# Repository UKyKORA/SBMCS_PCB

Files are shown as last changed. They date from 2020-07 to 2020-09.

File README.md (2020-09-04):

# Small Bot Motor Control Shield
This PCB makes building an advanced robot very simple. An onboard 32 bit ARM processor coordinates the control of 2 motors, as well as monitoring encoders on these motors for wheel odometry for the robot. There is a 9 axis IMU on the board to provide inertial odometry as well. a 5v @5A regulator provides enough power for most single board computers

### Board renders
<p>
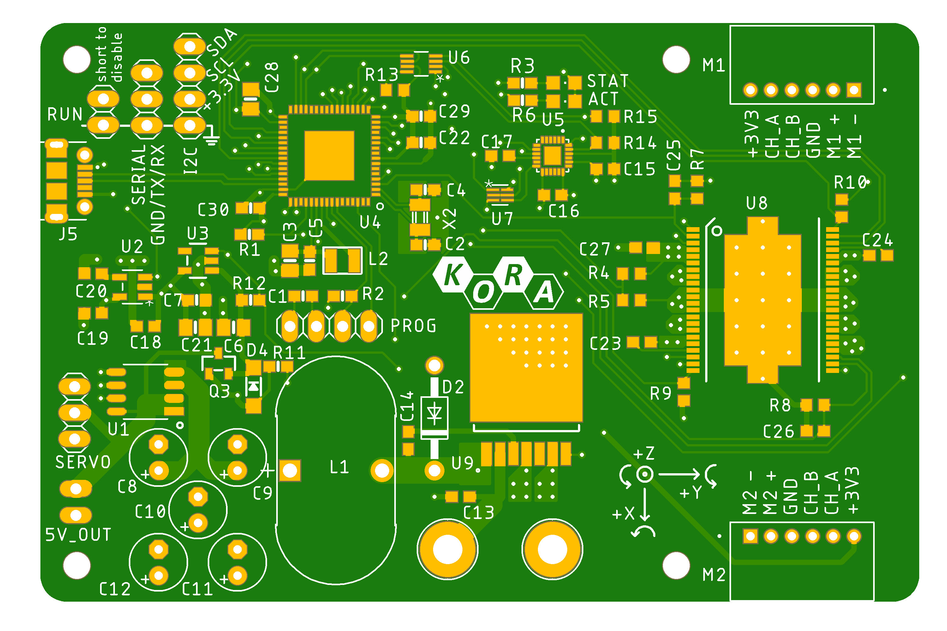
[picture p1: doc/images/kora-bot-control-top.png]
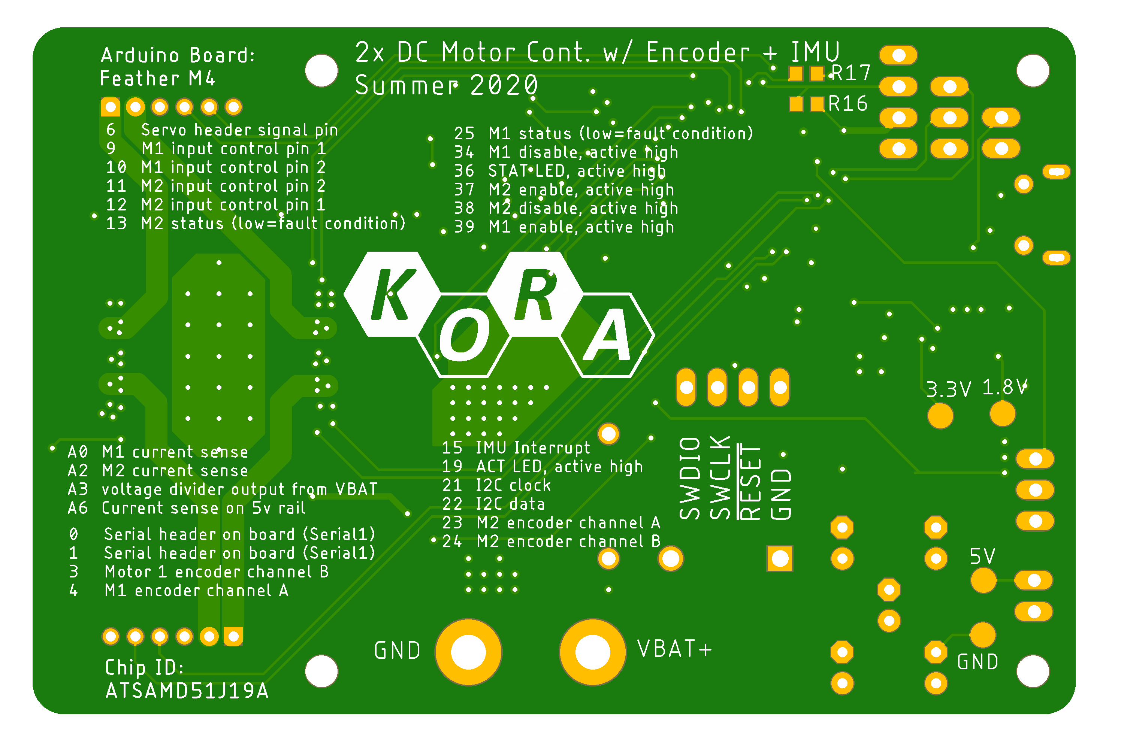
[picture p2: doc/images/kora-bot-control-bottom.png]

</p>

### Assembled boards
<p>

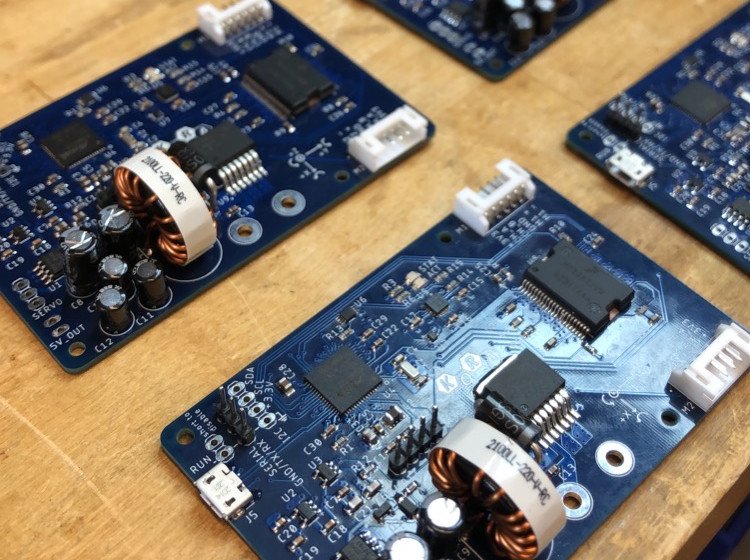
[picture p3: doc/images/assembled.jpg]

</p>

### Demonstration

[https://youtu.be/KzK6t1kKt98](https://youtu.be/KzK6t1kKt98)

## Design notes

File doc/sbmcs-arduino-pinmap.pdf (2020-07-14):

DEVICE PIN | ARDUINO PIN | NET | COMMENT
PA02 | A0 (14) | IM1_SENSE | motor 1 current sense, 0.24% of motor current is output across a 270 ohm resistor
PA05 | A1 (15) | INT | ICM20948 imu interrupt pin
PA06 | A5 (19) | ACT | ACT LED, active high
PA08 | 36 | STAT | STAT LED, active high
PA09 | 37 | EN/D4 | M2 enable pin, active high
PA10 | 38 | D3 | M2 disable pin, active high
PA11 | 39 | EN/D2 | M1 enable pin, active high
PA12 | 22 | SDA | I2C data
PA13 | 21 | SCL | I2C clock
PA14 | 4 | M1_ENC_A | motor 1 encoder channel a
PA17 | 25 | M1_STATUS | status (low=fault condition)
PA18 | 6 | SERVO | servo header signal pin
PA19 | 9 | IN1 | M1 input control pin 1
PA20 | 10 | IN2 | M1 input control pin 2
PA21 | 11 | IN4 | M2 input control pin 2
PA22 | 12 | IN3 | M2 input control pin 1
PA23 | 13 | M2_STATUS | status (low=fault condition)
PB01 | A6 (20) | I5V_SENSE | current sense on 5v rail
PB08 | A2 (16) | IM2_SENSE | motor 2 current sense, 0.24% of motor current is output across a 270 ohm resistor
PB09 | A3 (17) | VBAT_SENSE | voltage divider output from battery sensing.300k to vbat, 85k to gnd
PB10 | 34 | D1 | disable m1 (active high, high=motor pins are three stated
PB11 | 35 | M1_ENC_B | motor 1 encoder channel b
PB17 | 0 | SERIAL_RX | serial header on board (Serial1 object in arduino)
PB16 | 1 | SERIAL_TX | serial header on board (Serial1 object in arduino)
PB22 | 23 | M2_ENC_A | motor 2 encoder channel a
PB23 | 24 | M2_ENC_B | motor 2 encoder channel b

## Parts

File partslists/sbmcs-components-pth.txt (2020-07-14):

# through hole parts for korabot motor control shield

H1       MOUNT-PAD-ROUND2.8 MOUNT-PAD-ROUND2.8        2,8-PAD                holes              4
H2       MOUNT-PAD-ROUND2.8 MOUNT-PAD-ROUND2.8        2,8-PAD                holes              4

5V_OUT                      PINHD-1X2                 1X02                   pinhead            4
PROG                        PINHD-1X4                 1X04                   pinhead            1
I2C                         PINHD-1X4                 1X04                   pinhead            1
RUN                         PINHD-1X2                 1X02                   pinhead            4
SERIAL                      PINHD-1X3                 1X03                   pinhead            1
SERVO                       PINHD-1X3                 1X03                   pinhead            1
 M1       S6B-PH-K-S(LF)(SN) S6B-PH-K-S(LF)(SN)        JST_S6B-PH-K-S(LF)(SN) S6B-PH-K-S_LF__SN_ 2
 M2       S6B-PH-K-S(LF)(SN) S6B-PH-K-S(LF)(SN)        JST_S6B-PH-K-S(LF)(SN) S6B-PH-K-S_LF__SN_ 2

 C8       180uF              CPOL-USE2.5-6             E2,5-6                 adafruit           4
 C9       180uF              CPOL-USE2.5-6             E2,5-6                 adafruit           4
 C10      15uF               CPOL-USE2.5-6             E2,5-6                 adafruit           4
 C11      15uF               CPOL-USE2.5-6             E2,5-6                 adafruit           4
 C12      15uF               CPOL-USE2.5-6             E2,5-6                 adafruit           4

 L1       2100LL-220-V-RC    2100LL-220-V-RC           IND_2100LL_42_V        TI3VRegulator      4

 D2       1N4004             1N4004                    DO41-10                diode              4

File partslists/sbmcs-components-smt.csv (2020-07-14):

kora-bot-shield BOM
Item # | Ref. Des | Qty. | Mfg. Part # (DIGIKEY) | Description/Value | Package | Type
1 | STAT | 1 | LH R974-LP-1 | RED LED | 0805 | SMT
2 | ACT | 1 | LG R971-KN-1 | GREEN LED | 0805 | SMT
3 | C1,C5,C7,C22,C25,C26,C29,C30 | 8 | CL10A105KL8NNNC | 1 UF CER CAP | 0603 | SMT
4 | C2,C4 | 2 | C0603C220J8GAC7867 | 22 PF CER CAP | 0603 | SMT
5 | C3,C6,C21,C28 | 4 | C2012X5R1E106M125AB | 10 UF CER CAP | 0805 | SMT
6 | C13 | 1 | C1608X7R1H474K080AC | 0.47 UF CER CAP | 0603 | SMT
7 | C14,C20 | 2 | C1608C0G1V103J080AC | 10000 PF CER CAP | 0603 | SMT
8 | C15,C16,C17,C18,C27 | 5 | C0603C104Z3VACTU | 0.1 UF CER CAP | 0603 | SMT
9 | C19 | 1 | GRM188R71A225KE15D | 2.2 UF CER CAP | 0603 | SMT
10 | C23,C24 | 2 | CC0603KRX7R9BB333 | 0.033 UF CER CAP | 0603 | SMT
11 | U6 | 1 | PCA9306DCUR | IC TRNSLTR BIDIRECTIONAL | 8VSSOP | SMT
12 | U5 | 1 | ICM-20948 | IMU ACCEL/GYRO/COMPI2C/SPI | 24QFN | SMT
13 | U3 | 1 | AP2112K-3.3TRG1 | IC REG LINEAR 3.3V 600MA | SOT25 | SMT
14 | U2 | 1 | LP2985IM5-1.8/NOPB | IC REG LINEAR 1.8V 150MA | SOT23-5 | SMT
15 | U1 | 1 | ACS724LLCTR-05AB-T | SENSOR CURRENT HALL | 8-SOIC | SMT
16 | U8 | 1 | MC33932VWR2 | IC MOTOR DRIVER | 44HSOP | SMT
17 | L2 | 1 | CBC2518T100M | FIXED IND 10UH 680MA 468 MOHM | 1007 | SMT
18 | J5 | 1 | 1050170001 | CONN RCPT USB2.0 MICRO B SMD R/A | N/A | SMT
19 | U9 | 1 | LM2678SX-5.0/NOPB | IC REG BUCK 5V 5A | TO263-7 | SMT
20 | D4 | 1 | MBR120VLSFT3G | DIODE SCHOTTKY 20V 1A | SOD123FL | SMT
21 | U4 | 1 | ‎ATSAMD51J19A-MUT | IC MCU 32BIT 512KB FLASH | 64VQFN | SMT
22 | U7 | 1 | SN74LVC1T45DRLR | IC TRNSLTR BIDIRECTIONAL | 6SOT | SMT
23 | Q3 | 1 | DMP3056L-7 | MOSFET P-CH 30V 4.3A | SOT23 | SMT
24 | X2 | 1 | ECS-.327-12.5-34B-TR | CRYSTAL 32.7680KHZ 12.5PF SMD | N/A (3.2mm x 1.5mm) | SMT
25 | R1,R2,R12 | 3 | RC0603JR-0710KL | RES SMD 10K OHM 5% 1/10W | 0603 | SMT
26 | R3,R6 | 2 | RC0603JR-07470RL | RES SMD 470 OHM 5% 1/10W | 0603 | SMT
27 | R11 | 1 | RR0816P-104-D | RES SMD 100K OHM 0.5% 1/16W | 0603 | SMT
28 | R13 | 1 | RC0603FR-07200KL | RES SMD 200K OHM 1% 1/10W | 0603 | SMT
29 | R4 | 1 | RR0816P-304-D | RES SMD 300K OHM 0.5% 1/16W | 0603 | SMT
30 | R14,R15 | 2 | ERJ-3GEYJ222V | RES SMD 2.2K OHM 5% 1/10W | 0603 | SMT
31 | R7.R8,R9,R10 | 4 | CRGCQ0603F270R | RES SMD 270 OHM 1% | 0603 | SMT
32 | R5 | 1 | RC0603FR-0784K5L | RES SMD 84.5K OHM 1% 1/10W | 0603 | SMT

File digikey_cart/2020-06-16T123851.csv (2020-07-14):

Index | Quantity | Part Number | Manufacturer Part Number | Description | Customer Reference | Available | Backorder | Unit Price | Extended Price USD
1 | 11 | 475-1410-1-ND | LG R971-KN-1 | LED GREEN DIFFUSED 0805 SMD |  | 11 | 0 | 0.19100 | 2.10
2 | 11 | 475-1415-1-ND | LH R974-LP-1 | LED RED DIFFUSED 0805 SMD |  | 11 | 0 | 0.19100 | 2.10
3 | 11 | ATSAMD51J19A-MUTCT-ND | ATSAMD51J19A-MUT | IC MCU 32BIT 512KB FLASH 64VQFN |  | 11 | 0 | 4.34000 | 47.74
4 | 22 | 399-15378-1-ND | C0603C220J8GAC7867 | CAP CER 22PF 10V NP0 0603 |  | 22 | 0 | 0.12600 | 2.77
5 | 44 | 445-5985-1-ND | C2012X5R1E106M125AB | CAP CER 10UF 25V X5R 0805 |  | 44 | 0 | 0.26600 | 11.70
6 | 11 | 620-ACS724LLCTR-05AB-TCT-ND | ACS724LLCTR-05AB-T | SENSOR CURRENT HALL |  | 11 | 0 | 4.19500 | 46.15
7 | 22 | 399-7842-1-ND | C0603C103M5RACTU | CAP CER 10000PF 50V X7R 0603 |  | 22 | 0 | 0.03500 | 0.77
8 | 11 | 445-5952-1-ND | C1608X7R1H474K080AC | CAP CER 0.47UF 50V X7R 0603 |  | 11 | 0 | 0.19000 | 2.09
9 | 22 | 311-1429-1-ND | CC0603KRX7R9BB333 | CAP CER 0.033UF 50V X7R 0603 |  | 22 | 0 | 0.05800 | 1.28
10 | 11 | 296-20629-1-ND | SN74LVC1T45DRLR | IC TRNSLTR BIDIRECTIONAL 6SOT |  | 11 | 0 | 0.49500 | 5.45
11 | 11 | MBR120VLSFT3GOSCT-ND | MBR120VLSFT3G | DIODE SCHOTTKY 20V 1A SOD123FL |  | 11 | 0 | 0.31200 | 3.43
12 | 11 | LM2678SX-5.0/NOPBCT-ND | LM2678SX-5.0/NOPB | IC REG BUCK 5V 5A TO263-7 |  | 11 | 0 | 5.23600 | 57.60
13 | 11 | WM1399CT-ND | 1050170001 | CONN RCPT USB2.0 MICRO B SMD R/A |  | 11 | 0 | 0.80100 | 8.81
14 | 11 | 587-1613-1-ND | CBC2518T100M | FIXED IND 10UH 680MA 468 MOHM |  | 11 | 0 | 0.20700 | 2.28
15 | 11 | 568-15069-1-ND | MC33932VWR2 | IC MOTOR DRIVER PAR 44HSOP |  | 11 | 0 | 13.03800 | 143.42
16 | 11 | XC1617CT-ND | ECS-.327-12.5-34B-TR | CRYSTAL 32.7680KHZ 12.5PF SMD |  | 11 | 0 | 0.44800 | 4.93
17 | 11 | 490-4520-1-ND | GRM188R71A225KE15D | CAP CER 2.2UF 10V X7R 0603 |  | 11 | 0 | 0.18500 | 2.04
18 | 11 | DMP3056L-7DICT-ND | DMP3056L-7 | MOSFET P-CH 30V 4.3A SOT23 |  | 11 | 0 | 0.31300 | 3.44
19 | 11 | 296-17988-1-ND | PCA9306DCUR | IC TRNSLTR BIDIRECTIONAL 8VSSOP |  | 11 | 0 | 0.58100 | 6.39
20 | 11 | AP2112K-3.3TRG1DICT-ND | AP2112K-3.3TRG1 | IC REG LINEAR 3.3V 600MA SOT25 |  | 11 | 0 | 0.35500 | 3.91
21 | 11 | 1428-1123-1-ND | ICM-20948 | IMU ACCEL/GYRO/COMPI2C/SPI 24QFN |  | 11 | 0 | 6.26700 | 68.94
22 | 33 | 311-10KGRCT-ND | RC0603JR-0710KL | RES SMD 10K OHM 5% 1/10W 0603 |  | 33 | 0 | 0.01900 | 0.63
23 | 22 | 311-470GRCT-ND | RC0603JR-07470RL | RES SMD 470 OHM 5% 1/10W 0603 |  | 22 | 0 | 0.01900 | 0.42
24 | 11 | RR08P100KDCT-ND | RR0816P-104-D | RES SMD 100K OHM 0.5% 1/16W 0603 |  | 11 | 0 | 0.09300 | 1.02
25 | 11 | 311-200KHRCT-ND | RC0603FR-07200KL | RES SMD 200K OHM 1% 1/10W 0603 |  | 11 | 0 | 0.02300 | 0.25
26 | 11 | RR08P300KDCT-ND | RR0816P-304-D | RES SMD 300K OHM 0.5% 1/16W 0603 |  | 11 | 0 | 0.09300 | 1.02
27 | 22 | P2.2KGCT-ND | ERJ-3GEYJ222V | RES SMD 2.2K OHM 5% 1/10W 0603 |  | 22 | 0 | 0.04500 | 0.99
28 | 11 | 311-84.5KHRCT-ND | RC0603FR-0784K5L | RES SMD 84.5K OHM 1% 1/10W 0603 |  | 11 | 0 | 0.02300 | 0.25
29 | 55 | 399-1100-1-ND | C0603C104Z3VACTU | CAP CER 0.1UF 25V Y5V 0603 |  | 55 | 0 | 0.03200 | 1.76
30 | 88 | 1276-1861-1-ND | CL10A105KL8NNNC | CAP CER 1UF 35V X5R 0603 |  | 88 | 0 | 0.12900 | 11.35
31 | 22 | LP2985IM5-1.8/NOPBCT-ND | LP2985IM5-1.8/NOPB | IC REG LINEAR 1.8V 150MA SOT23-5 |  | 22 | 0 | 0.66700 | 14.67
32 | 44 | A129681CT-ND | CRGCQ0603F270R | CRGCQ 0603 270R 1% |  | 44 | 0 | 0.03000 | 1.32
33 | 22 | 1189-3642-ND | 25ZLQ180MEFC6.3X11 | CAP ALUM 180UF 20% 25V T/H |  | 22 | 0 | 0.20700 | 4.55
34 | 33 | P15801CT-ND | EEA-GA1E150H | CAP ALUM 15UF 20% 25V RADIAL |  | 33 | 0 | 0.18500 | 6.11
35 | 11 | 2100LL-220-V-RC-ND | 2100LL-220-V-RC | FIXED IND 22UH 7.5A 12 MOHM TH |  | 11 | 0 | 3.20900 | 35.30
36 | 11 | 1655-1921-1-ND | 90SQ045TA | DIODE SCHOTTKY 45V 9A DO201AD |  | 11 | 0 | 0.34000 | 3.74
37 | 22 | 455-1723-ND | S6B-PH-K-S(LF)(SN) | CONN HEADER R/A 6POS 2MM |  | 22 | 0 | 0.28500 | 6.27

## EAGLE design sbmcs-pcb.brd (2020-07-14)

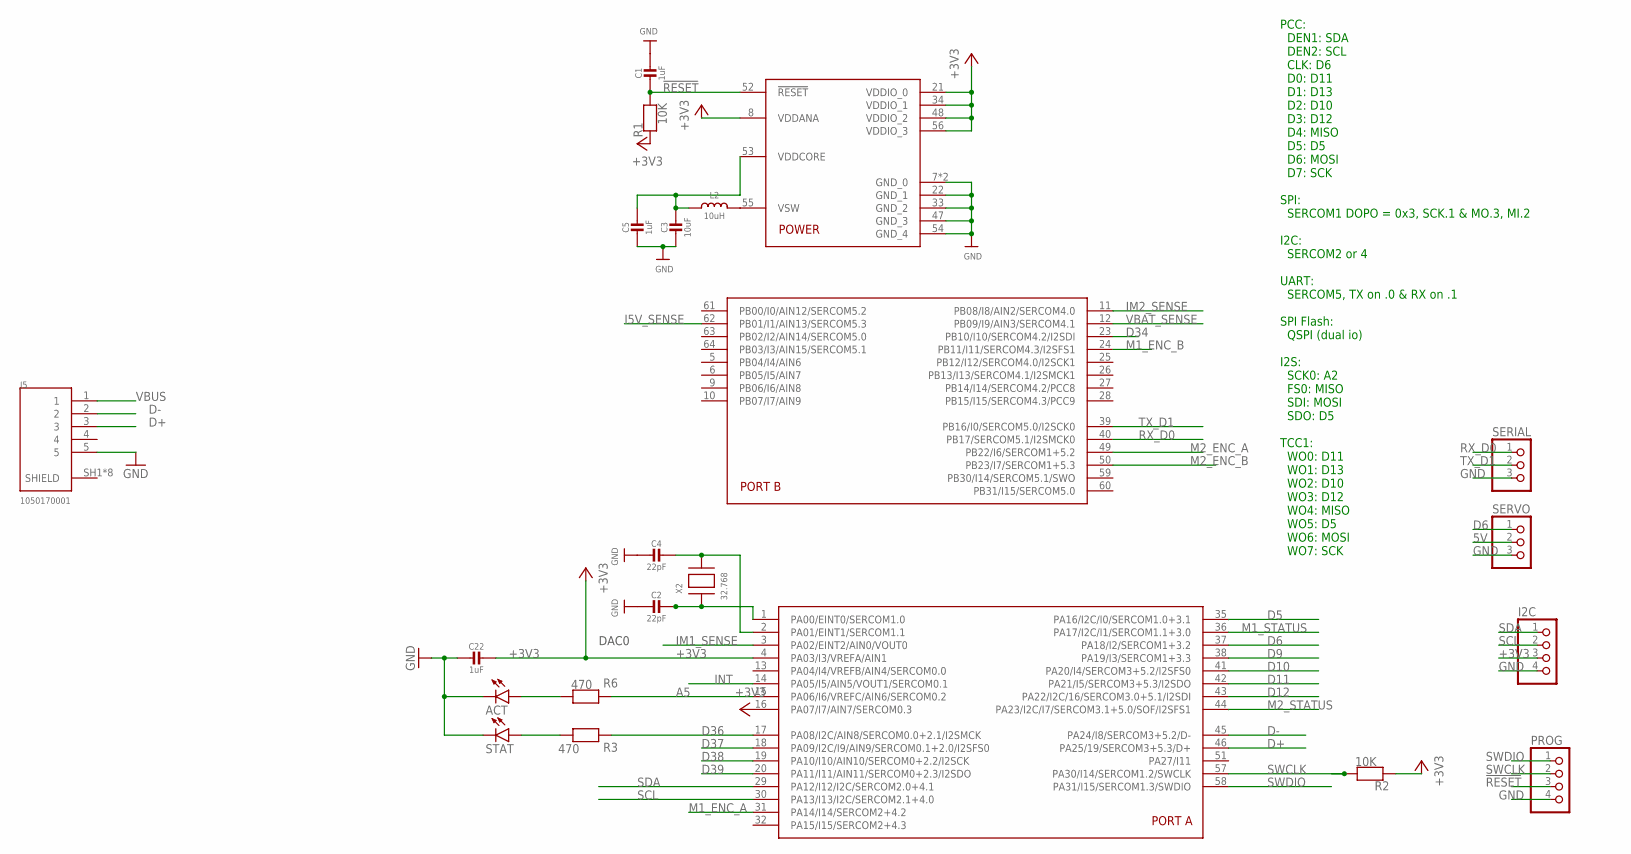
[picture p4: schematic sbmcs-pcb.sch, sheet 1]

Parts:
ACT: LEDCHIPLED_0805; CHIPLED_0805
C1, C5, C22: 1uF; 0603-NO
C2, C4: 22pF; 0603-NO
C3: 10uF; 0805-NO
I2C: PINHD-1X4; 1X04
J5: 1050170001; MOLEX_1050170001
L2: 10uH; INDUCTOR_1007
PROG: PINHD-1X4; 1X04
R1, R2: 10K; 0603-NO
R3, R6: 470; 0603-NO
SERIAL: PINHD-1X3; 1X03
SERVO: PINHD-1X3; 1X03
STAT: LEDCHIPLED_0805; CHIPLED_0805
U4: ATSAMD51J; PQFN64-1
X2: 32.768; XTAL3215

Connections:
5V: SERVO.2; also elsewhere on the board
!RESET: C1.2, PROG.3, R1.2, U4.52 (!RESET)
+3V3: C22.1, I2C.3, R1.1, R2.1, U4.4 (PA03/I3/VREFA/AIN1), U4.8 (VDDANA), U4.16 (PA07/I7/AIN7/SERCOM0.3), U4.21 (VDDIO_0), U4.34 (VDDIO_1), U4.48 (VDDIO_2), U4.56 (VDDIO_3); also elsewhere on the board
A5: R6.1, U4.15 (PA06/I6/VREFC/AIN6/SERCOM0.2)
D5: U4.35 (PA16/I2C/I0/SERCOM1.0+3.1)
D6: SERVO.1, U4.37 (PA18/I2/SERCOM1+3.2)
D9: U4.38 (PA19/I3/SERCOM1+3.3); also elsewhere on the board
D10: U4.41 (PA20/I4/SERCOM3+5.2/I2SFS0); also elsewhere on the board
D11: U4.42 (PA21/I5/SERCOM3+5.3/I2SDO); also elsewhere on the board
D12: U4.43 (PA22/I2C/16/SERCOM3.0+5.1/I2SDI); also elsewhere on the board
D34: U4.23 (PB10/I10/SERCOM4.2/I2SDI); also elsewhere on the board
D36: R3.1, U4.17 (PA08/I2C/AIN8/SERCOM0.0+2.1/I2SMCK)
D37: U4.18 (PA09/I2C/I9/AIN9/SERCOM0.1+2.0/I2SFS0); also elsewhere on the board
D38: U4.19 (PA10/I10/AIN10/SERCOM0+2.2/I2SCK); also elsewhere on the board
D39: U4.20 (PA11/I11/AIN11/SERCOM0+2.3/I2SDO); also elsewhere on the board
D+: J5.3, U4.46 (PA25/19/SERCOM3+5.3/D+)
D-: J5.2, U4.45 (PA24/I8/SERCOM3+5.2/D-)
GND: ACT.C, C1.1, C2.2, C3.2, C4.2, C5.2, C22.2, I2C.4, J5.5, PROG.4, SERIAL.3, SERVO.3, STAT.C, U4.7 (GND_0), U4.22 (GND_1), U4.33 (GND_2), U4.47 (GND_3), U4.54 (GND_4), U4.EXP (GND_0); also elsewhere on the board
I5V_SENSE: U4.62 (PB01/I1/AIN13/SERCOM5.3); also elsewhere on the board
IM1_SENSE: U4.3 (PA02/EINT2/AIN0/VOUT0); also elsewhere on the board
IM2_SENSE: U4.11 (PB08/I8/AIN2/SERCOM4.0); also elsewhere on the board
INT: U4.14 (PA05/I5/AIN5/VOUT1/SERCOM0.1); also elsewhere on the board
M1_ENC_A: U4.31 (PA14/I14/SERCOM2+4.2); also elsewhere on the board
M1_ENC_B: U4.24 (PB11/I11/SERCOM4.3/I2SFS1); also elsewhere on the board
M1_STATUS: U4.36 (PA17/I2C/I1/SERCOM1.1+3.0); also elsewhere on the board
M2_ENC_A: U4.49 (PB22/I6/SERCOM1+5.2); also elsewhere on the board
M2_ENC_B: U4.50 (PB23/I7/SERCOM1+5.3); also elsewhere on the board
M2_STATUS: U4.44 (PA23/I2C/I7/SERCOM3.1+5.0/SOF/I2SFS1); also elsewhere on the board
unnamed: R3.2, STAT.A
unnamed: ACT.A, R6.2
unnamed: C2.1, U4.1 (PA00/EINT0/SERCOM1.0), X2.P$1
unnamed: C4.1, U4.2 (PA01/EINT1/SERCOM1.1), X2.P$2
unnamed: L2.P$2 (2), U4.55 (VSW)
RX_D0: SERIAL.1, U4.40 (PB17/SERCOM5.1/I2SMCK0)
SCL: I2C.2, U4.30 (PA13/I13/I2C/SERCOM2.1+4.0); also elsewhere on the board
SDA: I2C.1, U4.29 (PA12/I12/I2C/SERCOM2.0+4.1); also elsewhere on the board
SWCLK: PROG.2, R2.2, U4.57 (PA30/I14/SERCOM1.2/SWCLK)
SWDIO: PROG.1, U4.58 (PA31/I15/SERCOM1.3/SWDIO)
TX_D1: SERIAL.2, U4.39 (PB16/I0/SERCOM5.0/I2SCK0)
VBAT_SENSE: U4.12 (PB09/I9/AIN3/SERCOM4.1); also elsewhere on the board
VBUS: J5.1; also elsewhere on the board
VDDCORE1: C3.1, C5.1, L2.P$1 (1), U4.53 (VDDCORE)

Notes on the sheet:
PCC: DEN1: SDA DEN2: SCL CLK: D6 D0: D11 D1: D13 D2: D10 D3: D12 D4: MISO D5: D5 D6: MOSI D7: SCK SPI: SERCOM1 DOPO = 0x3, SCK.1 & MO.3, MI.2 I2C: SERCOM2 or 4 UART: SERCOM5, TX on .0 & RX on .1 SPI Flash: QSPI (dual io) I2S: SCK0: A2 FS0: MISO SDI: MOSI SDO: D5 TCC1: WO0: D11 WO1: D13 WO2: D10 WO3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
DAC0

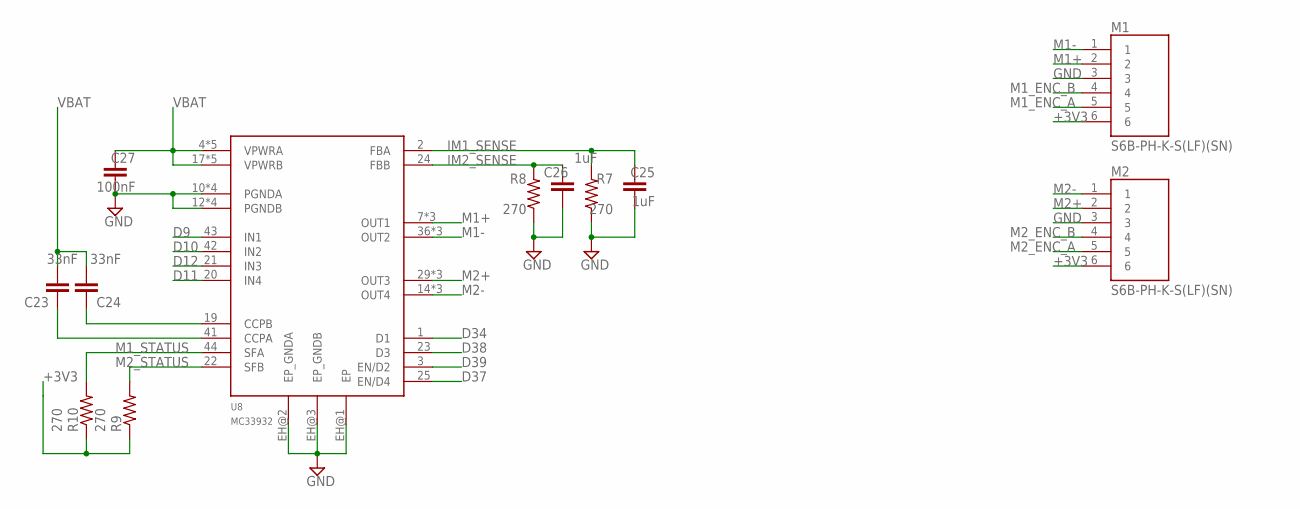
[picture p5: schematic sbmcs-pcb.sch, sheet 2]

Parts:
C23, C24: 33nF; C0603
C25, C26: 1uF; C0603
C27: 100nF; C0603
M1, M2: S6B-PH-K-S(LF)(SN); JST_S6B-PH-K-S(LF)(SN)
R7, R8, R9, R10: 270; R0603
U8: MC33932; HSOP44

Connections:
+3V3: M1.6, M2.6, R9.1, R10.1; also elsewhere on the board
D9: U8.43 (IN1); also elsewhere on the board
D10: U8.42 (IN2); also elsewhere on the board
D11: U8.20 (IN4); also elsewhere on the board
D12: U8.21 (IN3); also elsewhere on the board
D34: U8.1 (D1); also elsewhere on the board
D37: U8.25 (EN/D4); also elsewhere on the board
D38: U8.23 (D3); also elsewhere on the board
D39: U8.3 (EN/D2); also elsewhere on the board
GND: C25.1, C26.1, C27.1, M1.3, M2.3, R7.1, R8.1, U8.10 (PGNDA), U8.11 (PGNDA), U8.12 (PGNDB), U8.13 (PGNDB), U8.32 (PGNDB), U8.33 (PGNDB), U8.34 (PGNDA), U8.35 (PGNDA), U8.EH@1 (EP), U8.EH@2 (EP_GNDA), U8.EH@3 (EP_GNDB); also elsewhere on the board
IM1_SENSE: C25.2, R7.2, U8.2 (FBA); also elsewhere on the board
IM2_SENSE: C26.2, R8.2, U8.24 (FBB); also elsewhere on the board
M1+: M1.2, U8.7 (OUT1), U8.8 (OUT1), U8.9 (OUT1)
M1-: M1.1, U8.36 (OUT2), U8.37 (OUT2), U8.38 (OUT2)
M1_ENC_A: M1.5; also elsewhere on the board
M1_ENC_B: M1.4; also elsewhere on the board
M1_STATUS: R10.2, U8.44 (SFA); also elsewhere on the board
M2+: M2.2, U8.29 (OUT3), U8.30 (OUT3), U8.31 (OUT3)
M2-: M2.1, U8.14 (OUT4), U8.15 (OUT4), U8.16 (OUT4)
M2_ENC_A: M2.5; also elsewhere on the board
M2_ENC_B: M2.4; also elsewhere on the board
M2_STATUS: R9.2, U8.22 (SFB); also elsewhere on the board
unnamed: C24.1, U8.41 (CCPA)
unnamed: C23.1, U8.19 (CCPB)
VBAT: C23.2, C24.2, C27.2, U8.4 (VPWRA), U8.5 (VPWRA), U8.6 (VPWRA), U8.17 (VPWRB), U8.18 (VPWRB), U8.26 (VPWRB), U8.27 (VPWRB), U8.28 (VPWRB), U8.39 (VPWRA), U8.40 (VPWRA); also elsewhere on the board

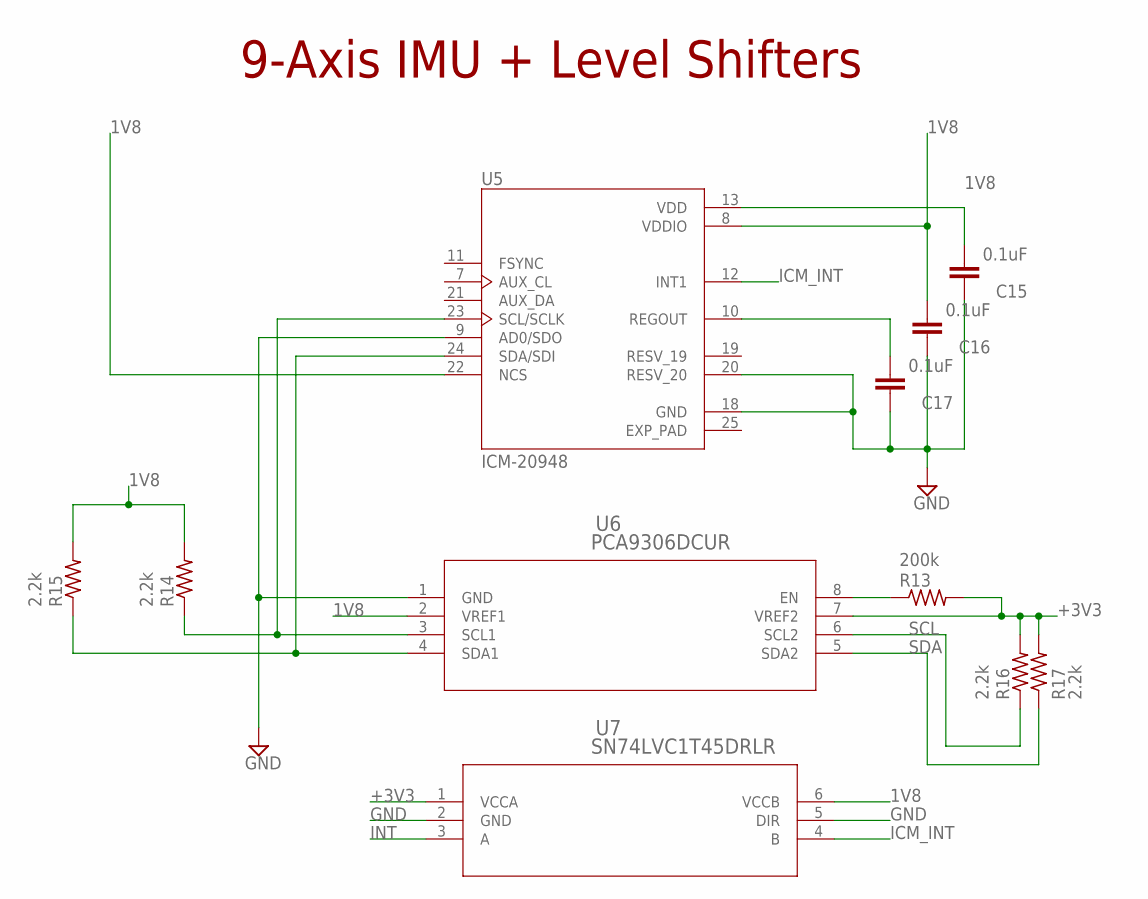
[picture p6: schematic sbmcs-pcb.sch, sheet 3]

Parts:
C15, C16, C17: 0.1uF; C0603
R13: 200k; R0603
R14, R15, R16, R17: 2.2k; R0603
U5: ICM-20948; QFN40P300X300X105-25N
U6: PCA9306DCUR; DCU8
U7: SN74LVC1T45DRLR; DRL6

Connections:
1V8: C15.2, C16.2, R14.2, R15.2, U5.8 (VDDIO), U5.13 (VDD), U5.22 (NCS), U6.2 (VREF1), U7.6 (VCCB); also elsewhere on the board
+3V3: R13.2, R16.2, R17.2, U6.7 (VREF2), U7.1 (VCCA); also elsewhere on the board
EXP_PAD: U5.25 (EXP_PAD)
GND: C15.1, C16.1, C17.1, U5.9 (AD0/SDO), U5.18 (GND), U5.20 (RESV_20), U6.1 (GND), U7.2 (GND), U7.5 (DIR); also elsewhere on the board
ICM_INT: U5.12 (INT1), U7.4 (B)
INT: U7.3 (A); also elsewhere on the board
unnamed: R13.1, U6.8 (EN)
unnamed: C17.2, U5.10 (REGOUT)
unnamed: R14.1, U5.23 (SCL/SCLK), U6.3 (SCL1)
unnamed: R15.1, U5.24 (SDA/SDI), U6.4 (SDA1)
SCL: R16.1, U6.6 (SCL2); also elsewhere on the board
SDA: R17.1, U6.5 (SDA2); also elsewhere on the board

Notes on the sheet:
9-Axis IMU + Level Shifters

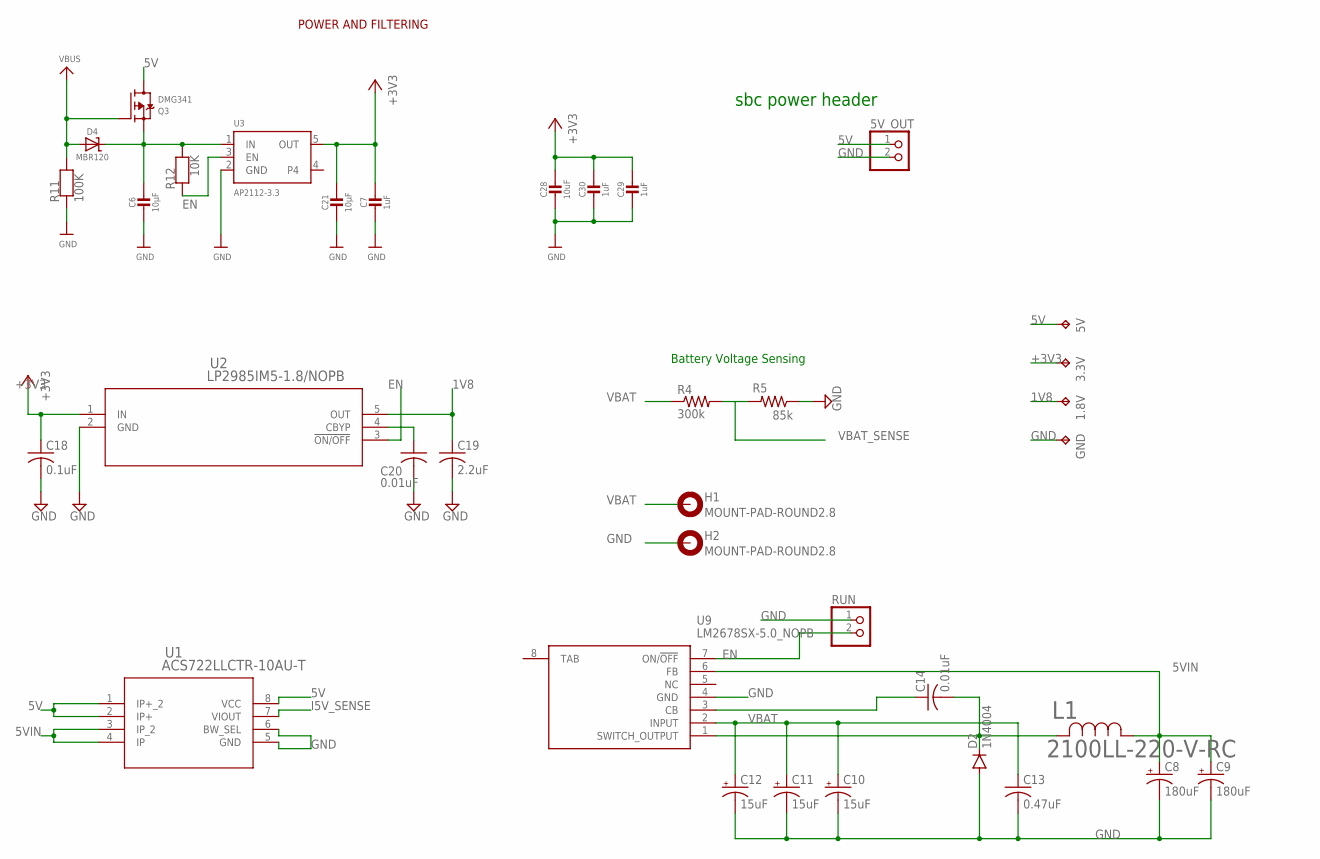
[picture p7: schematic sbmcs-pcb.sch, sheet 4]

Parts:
1.8V, 3.3V, 5V: TPTP20R; TP20R
5V_OUT: PINHD-1X2; 1X02
C6, C21: 10µF; 0805-NO
C7, C29, C30: 1uF; 0603-NO
C8, C9: 180uF; E2,5-6
C10, C11, C12: 15uF; E2,5-6
C13: 0.47uF; C0603
C14, C20: 0.01uF; C0603
C18: 0.1uF; C0603
C19: 2.2uF; C0603
C28: 10uF; 0805-NO
D2: 1N4004; DO41-10
D4: MBR120; SOD-123
GND: TPTP20R; TP20R
H1, H2: MOUNT-PAD-ROUND2.8; 2,8-PAD
L1: 2100LL-220-V-RC; IND_2100LL_42_V
Q3: DMG341; SOT23-R
R4: 300k; R0603
R5: 85k; R0603
R11: 100K; 0603-NO
R12: 10K; 0603-NO
RUN: PINHD-1X2; 1X02
U1: ACS722LLCTR-10AU-T; SOICN-8_ALM
U2: LP2985IM5-1.8/NOPB; MF05A
U3: AP2112-3.3; SOT23-5
U9: LM2678SX-5.0_NOPB; KTW0007B

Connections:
1V8: 1.8V.TP, C19.1, U2.5 (OUT); also elsewhere on the board
5V: 5V.TP, 5V_OUT.1, Q3.3 (D), U1.1 (IP+_2), U1.2 (IP+), U1.8 (VCC); also elsewhere on the board
5VIN: C8.+, C9.+, L1.1, U1.3 (IP_2), U1.4 (IP), U9.6 (FB)
+3V3: 3.3V.TP, C7.1, C18.1, C21.1, C28.1, C29.1, C30.1, U2.1 (IN), U3.5 (OUT); also elsewhere on the board
EN: R12.1, RUN.2, U2.3 (!ON/OFF), U3.3 (EN), U9.7 (ON/!OFF)
GND: 5V_OUT.2, C6.2, C7.2, C8.-, C9.-, C10.-, C11.-, C12.-, C13.2, C18.2, C19.2, C20.2, C21.2, C28.2, C29.2, C30.2, D2.A, GND.TP, H2.B2,8, R5.1, R11.1, RUN.1, U1.5 (GND), U1.6 (BW_SEL), U2.2 (GND), U3.2 (GND), U9.4 (GND); also elsewhere on the board
I5V_SENSE: U1.7 (VIOUT); also elsewhere on the board
unnamed: C20.1, U2.4 (CBYP)
unnamed: C14.1, U9.3 (CB)
unnamed: C14.2, D2.C, L1.2, U9.1 (SWITCH_OUTPUT)
VBAT: C10.+, C11.+, C12.+, C13.1, H1.B2,8, R4.1, U9.2 (INPUT); also elsewhere on the board
VBAT_SENSE: R4.2, R5.2; also elsewhere on the board
VBUS: D4.A, Q3.1 (G), R11.2; also elsewhere on the board
VHI: C6.1, D4.C, Q3.2 (S), R12.2, U3.1 (IN)

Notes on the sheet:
Battery Voltage Sensing
POWER AND FILTERING
sbc power header

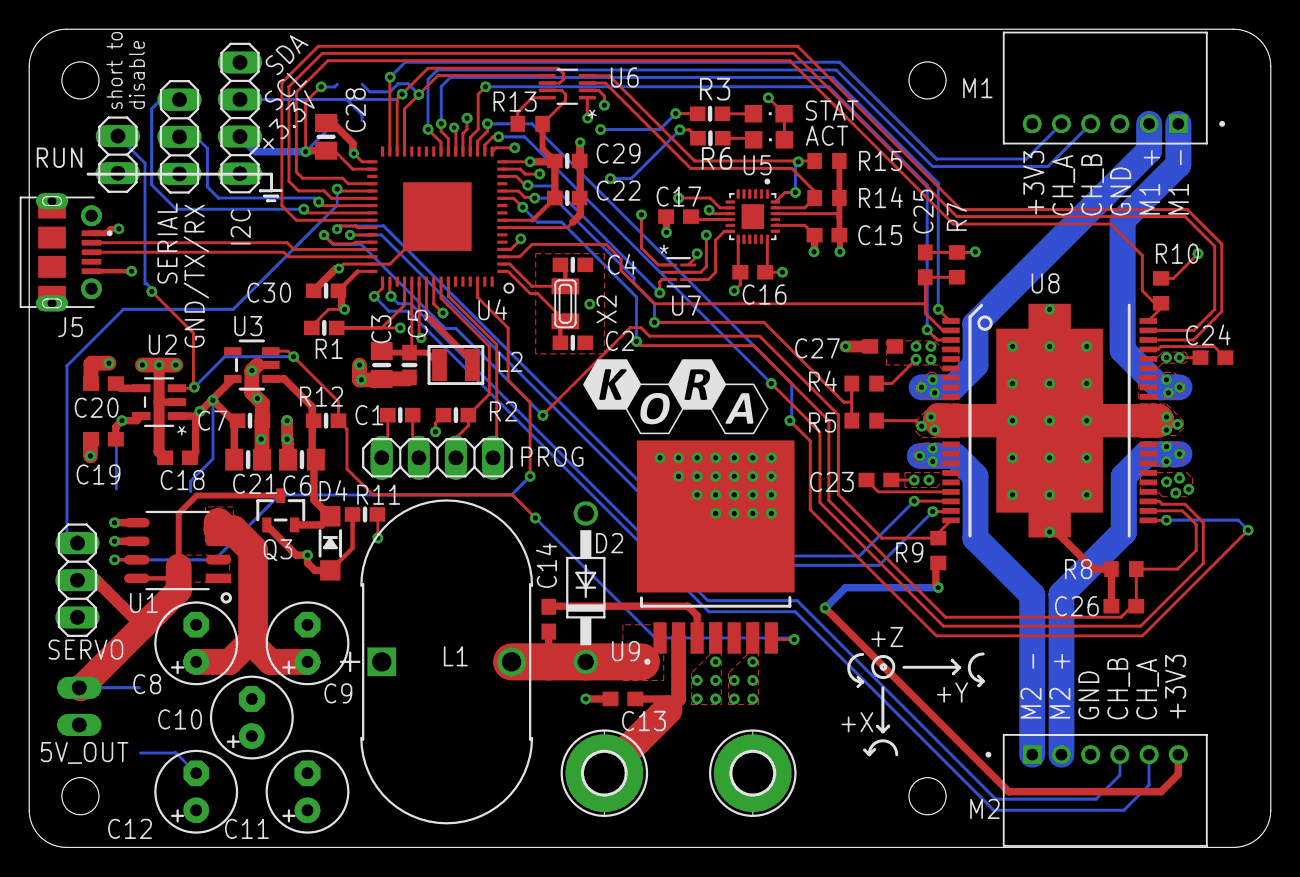
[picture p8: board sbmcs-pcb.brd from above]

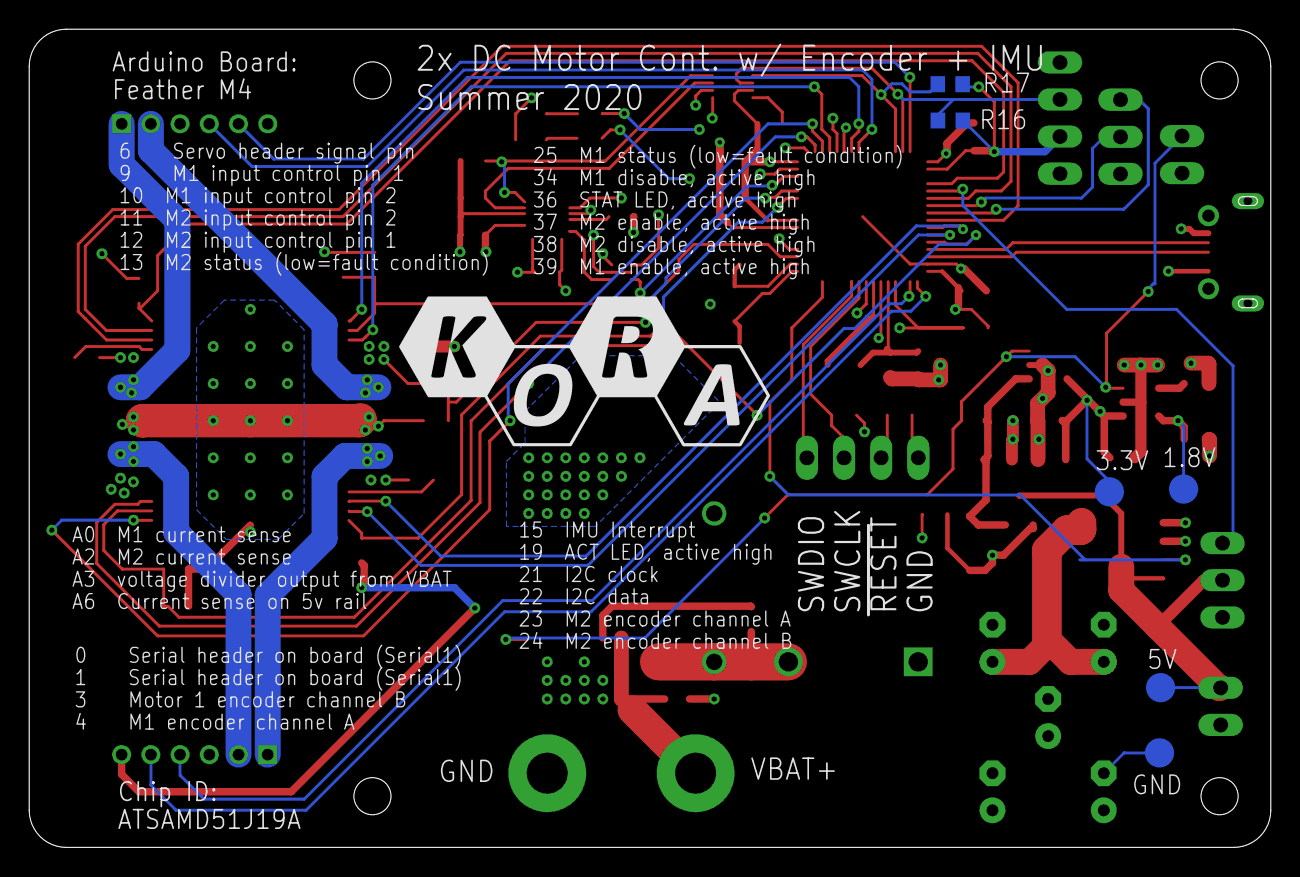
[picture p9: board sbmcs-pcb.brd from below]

Board: 4 copper layers, 85.0 x 56.0 mm, 79 parts (6 on the bottom side), 60 nets.

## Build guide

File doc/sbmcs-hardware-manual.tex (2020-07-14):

\documentclass{article}
\usepackage[utf8]{inputenc}

\usepackage{url}
\usepackage{float}
\usepackage{natbib}
\usepackage{authblk}
\usepackage{graphicx}
\usepackage{listings}
\usepackage{fullpage}
\usepackage{hyperref}
\hypersetup{
    colorlinks=true,
    linkcolor=blue,
    filecolor=magenta,      
    urlcolor=cyan,
}
\title{Small Bot Motor Control Shield Hardware Manual}
\author[1]{Matt Ruffner}
\author[1]{Damien Lawhorn}
\author[1]{Josh Ashley}
\affil[1]{University of Kentucky}
\date{July 10, 2020}
\setcounter{Maxaffil}{0}
\renewcommand\Affilfont{\itshape\small}
\begin{document}

\maketitle
\tableofcontents
%\newpage
\listoffigures
\listoftables
%\newpage

\section{Introduction}
This document contains information relevant to the design of the Small Bot Motor Control Shield (SBMCS). The SBMCS is being developed by the Kentcuky Organization of Robotics and Automation (KORA) student led club at the University of Kentucky.

\appendix
\label{sec:appa}

\section{SBMCS Arduino Pin Assignment}
\begin{figure}[H]
    \centering
    
    \label{fig:sbmcs-arduino-pinmap}
\end{figure}

\section{Feather M4 Arduino Reference}
Courtesy of Adafruit Industries
\begin{figure}[H]
    \centering
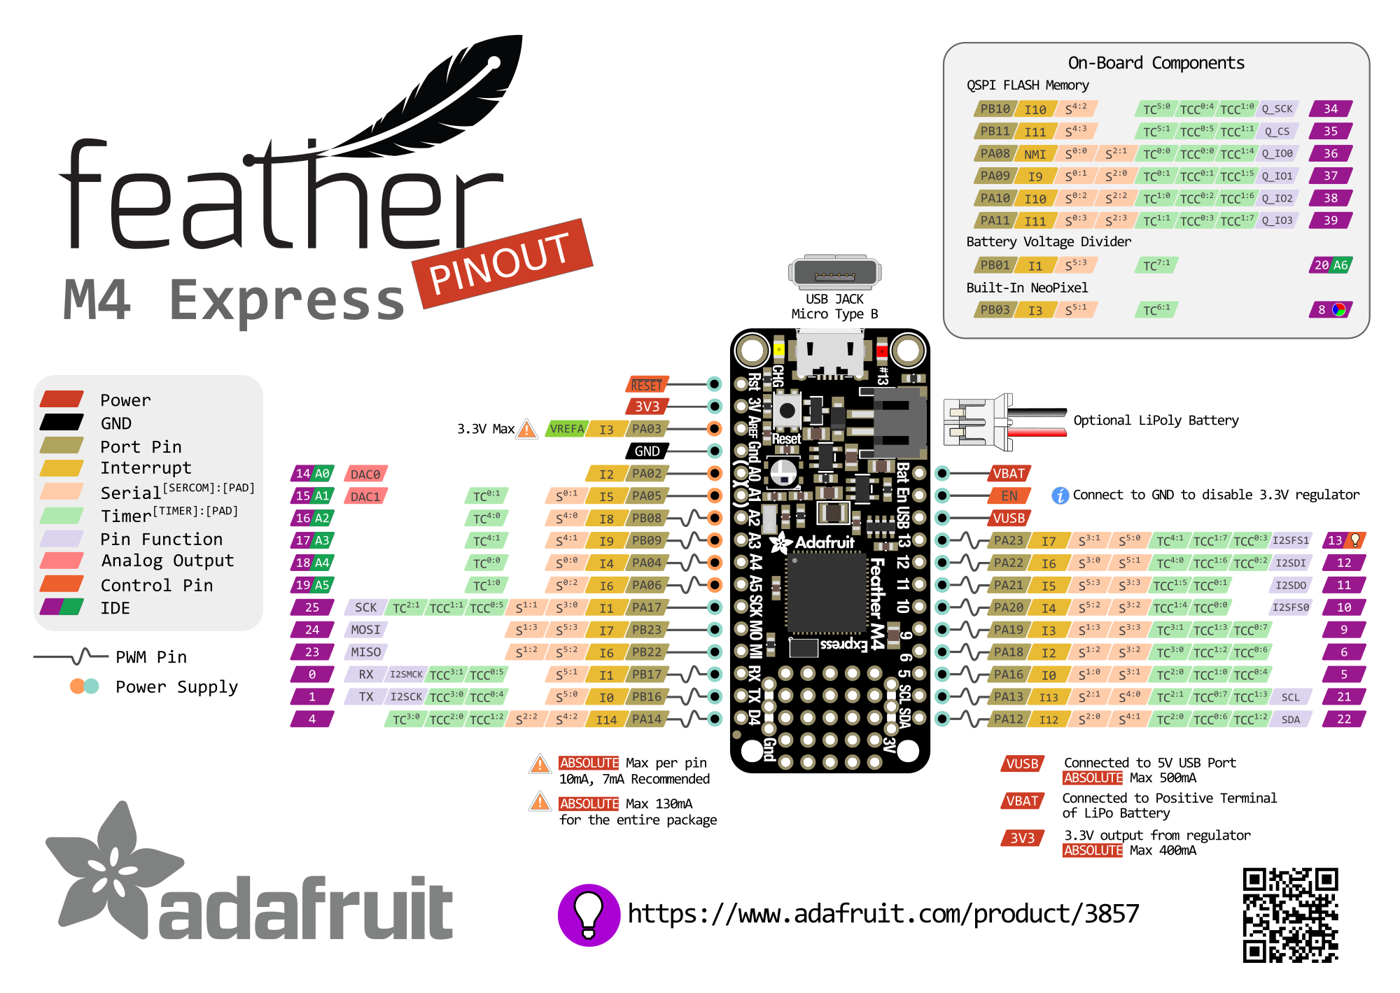
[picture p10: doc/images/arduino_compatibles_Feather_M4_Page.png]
    
    \label{fig:m4-pinout}
\end{figure}

\end{document}

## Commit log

2020-07-14 initial commit of v1 SBMCS
    * Eagle files for schematic and board layout
    * SMT and PTH partslists
    * Digikey cart with board components
    * Top/bottom renderings of board
    * Gerbers
    * Outline of SBMCS hardware manual
    [2020-06-16T123851.csv, sbmcs-components-smt.csv, sbmcs-pcb.brd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]
2020-09-04 add image of assembled board

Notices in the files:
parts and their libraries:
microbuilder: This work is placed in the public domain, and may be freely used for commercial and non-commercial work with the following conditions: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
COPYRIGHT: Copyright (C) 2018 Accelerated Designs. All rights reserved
